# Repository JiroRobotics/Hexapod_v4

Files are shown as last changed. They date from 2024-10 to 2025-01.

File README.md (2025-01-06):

# Hexapod v4
Check out the YouTube video: https://youtu.be/cIIxmBn0WJ8

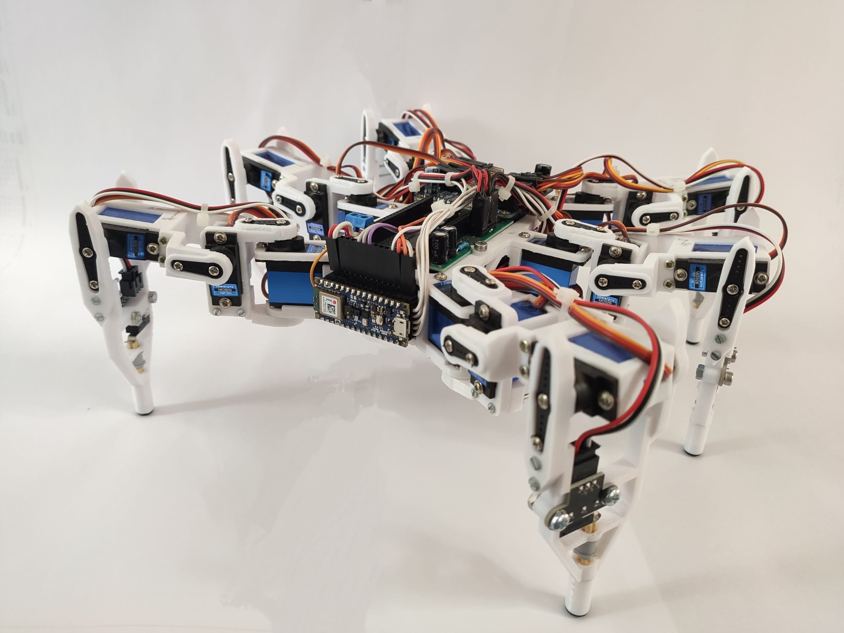
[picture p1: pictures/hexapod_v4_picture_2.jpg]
Hexapod prototype


## Quickstart

1. Build your Hexapod
2. Download this repository as well as all other necessary libraries
3. Change angle() and angleFloat() in Leg.cpp to use the correct pulse lengths for your servos. The current configuration works for (one type of) MG92b servos.
4. The isReachable() method of the Leg class is highly dependent on the geometry of your robot, therefore it also needs to be changed if you don't use the CAD files.
5. Take a close look at Config.h and change all values accordingly. You'll need to change all pins as well as all measurements.
6. Also change the addresses of your servo drivers to the correct hex value.
7. Double check your wiring and provide the Leg() constructors in Hexapod_v4.ino with the correct PWM Module.
8. Figure out the offsets for each servo. If you write an angle of 90° to a servo, the corresponding joint should form a right angle. Keep these offsets as low as possible (-10° to 10°). You might also need to unscrew the joint and mount it at a different angle.
9. The code works well on an Arduino Nano 33 BLE Sense. If you use other, less capable Arduinos like Nano 33 IOT, you might need to increase the periodMS setting in Config.h, until the Arduino is able to calculate everything in this time frame.

## Background

Hexapods are six legged robots. They possess the ability to walk in any direction, each leg (in this case) with three joints resulting in a total of 18 degrees of freedom. In addition, their body can turn and rotate in any direction, making this type of legged robot extremely flexible. But six legs also allow for fast, statically determined walking gates, i.e. lifting three legs each step while the three other legs stay on the ground. This removes the challenge of balancing during one step. 

As written in the title, this project is my fourth hexapod robot. It uses largely the same hardware as the previous generation but the code was rewritten entirely. The ReadMe was written in order to provide support and document the whole project. Feel free to contact me for questions/suggestions/improvements.

## Requirements

In addition to the code in this repository, you will need two additional libraries, "Adafruit_PWMServoDriver.h" and "Arduino_BMI270_BMM150.h" for the servo driver and the IMU (only Arduino Nano 33 BLE) respectively. Just clone this repository and adjust the code to suit your robot. Almost all important constants are specified in Config.h, but a few other things also need to be changed, e.g. the constraints for leg movement (more on that later) or the servo pulse lengths. This ReadMe is written in a way which should allow you to follow my thought process during the creation of this robot. It is quite extensive so don't be afraid to skip some parts. The code is mathematically challenging, so you should be familiar with the basics of inverse kinematics and coordinate transformation in order to understand everything.

## Hardware

The robot is comprised of a 3D-printed body and six legs. The four corner legs are turned by an angle of 30° relative to the middle legs, thus requiring more complex code. Consider mounting the corner legs parallel to the middle legs in your project to avoid the need for more coordinate transformation in your code. 
Each leg consists of three joints and three links refered to as coxa, femur and tibia. Each joint is directly screwed to the servo on one side and on the other a tiny bearing is used to reduce friction, add strength and avoid wear and tear.
The coxa link incorporates a limit switch to detect whether the leg is touching the ground. If the leg is touching the ground, the weight doesn't rest on the switch but the surrounding structure.

As for the electronics, the robot is powered by 18 TowerPro MG92b servo motors. As the name suggests, these servos use metal gears as well as a small bearing on the shaft, making them pretty robust and ideal for the use in this application. Nine servos are each connected to an [Adafruit PCA9685 16-Channel Servo Driver](https://learn.adafruit.com/16-channel-pwm-servo-driver/downloads), resulting in one servo driver for each side (left/right) of the robot. Make sure to use the original Adafruit servo driver since the cheaper alternatives often use a low-quality MOSFET which is not suitable for providing enough current for 18 servo motors. They are often marketed as LED-drivers only.
A 10V 1000uF capacitor is used as suggested by Adafruit to avoid voltage dips when all servos move at the same time, minimizing the chance for brownouts. The two servo drivers are connected to an Arduino Nano 33 BLE Sense Rev2 via I2C. Make sure that you power the servo motors not through the Arduino but directly from the power source (using the V+ pin on the board). In this robot, I used a rechargeable 6V 3000mAh NiMH-Battery which provides plenty of power while lasting a good 20-30 minutes. A large switch on the back of the robot acts as the killswitch, immediatly cutting power from the Arduino as well as the drivers.
The six limit switches are also connected to the Arduino using six of the GPIOs. Additionally, an ESP32 (potentionally with an integrated camera module) can be placed on top of the robot to stream a video feed of what the robot sees directly on your phone.

## Software
The code for this robot was entirely written in C++ (or rather the Arduino version of C++). The rough structure is as follows:
* A Leg class which handles the inverse kinematics of each leg (only the movement in the local coordinate system of each leg). This class also checks whether or not a (x, y, z) point is reachable for the end point of the leg and if the leg is touching the ground.
* A Hexapod class which is an aggregation of six leg instances. This class covers all movement patterns (such as crab walk, translation and rotation on the spot, turning, ...).
* The main Arduino programm, which is comprised of the setup() and the loop()-part. The setup()-part is run once and covers all the initialization of the servo drivers as well as setting pin modes, starting the IMU and so on. The loop() function is coded so that it is executed every 10ms, giving the hexapod an update rate of 100Hz. This means that the leg positions are calculated and the legs are moved to their positions every 10ms or 100 times a second. Running a fixed update rate allows for more flexible movement as a step is not necessarily excecuted as a whole and other movements can be superimposed.

Let's take a look at the math-heavy challenges for this project:

### Inverse Kinematics Of One Leg
**Goal:** given a point (x, y, z) in the local coordinate frame of the leg, calculate the joint angles of the three servo motors so that the end point of the leg reaches the desired point
First, we assume that the point is valid/reachable (more on that later). Next we will have to take a look at the coordinate system and how the leg is positioned in it.

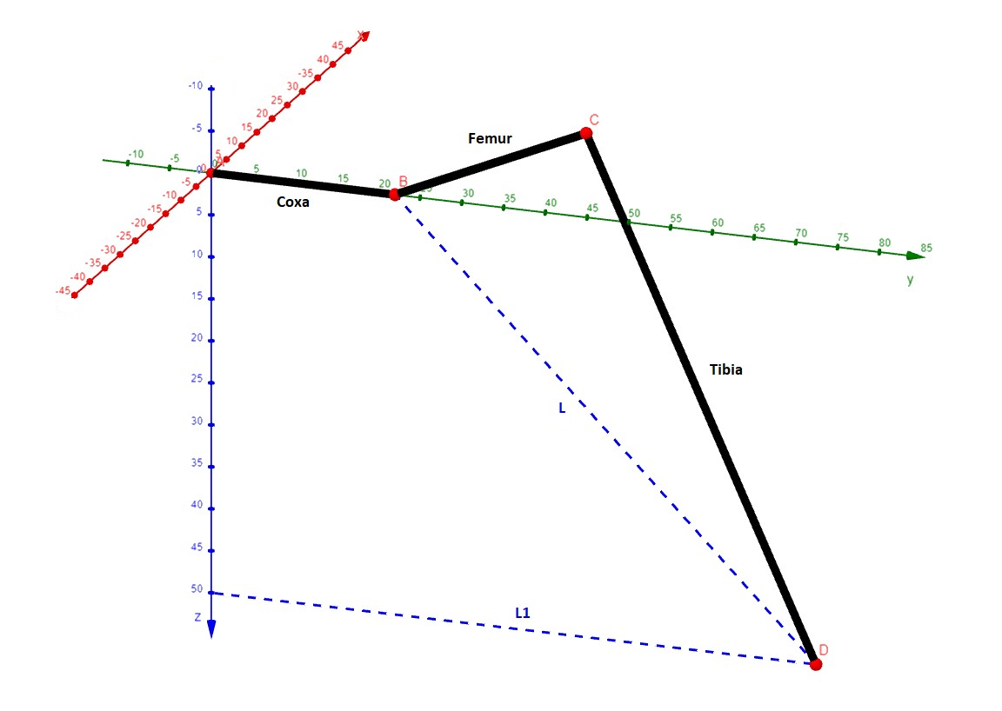
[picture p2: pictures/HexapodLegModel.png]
Image of a leg model and the coordinate system as well as L and L1


A, B and C are the coxa, femur and tibia joints while D is the desired point given in (x, y, z) coordinates. It becomes apparent that the coxa angle is only dependent on the x and y and can be calculated by using the atan2(y, x) function. Note that this returns radians, so you might need to convert to degrees. Perhaps you also need to mirror the value using map(), depending on the servo orientation.
The values for the femur and tibia joint are a bit more complex. First, we need to calculate two distances: L1 and L. L1 is simply the distance from the z-axis to point D, which can be found using the pythagorean theorem. L1 can than be used to calculate L, which is the distance from B to D. Again, it is found by using the pythagorean theorem. Now, by applying the law of cosine, the angles of the triangle BCD can be found. Make sure to shift/mirror the values to match the orientation of the servos. The code for calculating all three angles is as follows:

```
float coxaAngle = atan2(yValue, xValue) * 180 / PI;
coxaAngle = map(coxaAngle, 0, 180, 180, 0);
float femurAngle = (acos(zValue / L) + acos((tibiaLength * tibiaLength - femurLength * femurLength - L * L) / (-2 * femurLength * L))) * 180 / PI;
float tibiaAngle = (acos((L * L - tibiaLength * tibiaLength - femurLength * femurLength) / (-2 * tibiaLength * femurLength))) * 180 / PI;
```

The last thing to do is to actually move the servos. This can be achieved by calling the following line:

```
servoDriver.setPWM(pinCoxa, 0, angleFloat(coxaAngle + offsetCoxa));
```
angleFloat() is a function to convert the angle in degrees to the corresponding pulse width of the PWM signal (also described in the Adafruit Servo Driver documentation). The values in angleFloat() have to be adjusted if another type of servo is used. offsetCoxa is the offset (in degrees) by which the (real) position of the leg differs compared to the ideal position. Find these values by assembling the robot, setting all servos to for example 90° and adjust the offsets until all joints are perfectly perpendicular.

### Calculating Valid Points
The leg can't reach every (x, y, z) point in 3D space. If we instruct the leg to move to an unreachable point, weird things can happen, potentionally even breaking the robot. Even if all points passed to the leg function _should_ be reachable, it is recommended to implement the following as a last safeguard:
The constrains for the coxaAngle parameter can be chosen by simply measuring how far the legs can rotate before hitting the neighboring leg rotating in the opposite direction. In this case, coxaAngle can only be in the interval [40°, 130°]
Instead of implementing constrains directly for tibiaAngle and femurAngle, we simply look at the L1 value and the z value and define an area in which L1 and z have to be to be valid. This area can be found mathematically or approximated using a CAD model (as shown in the image). By comparing L1 and z to the upper and lower bound, each point can be verified.

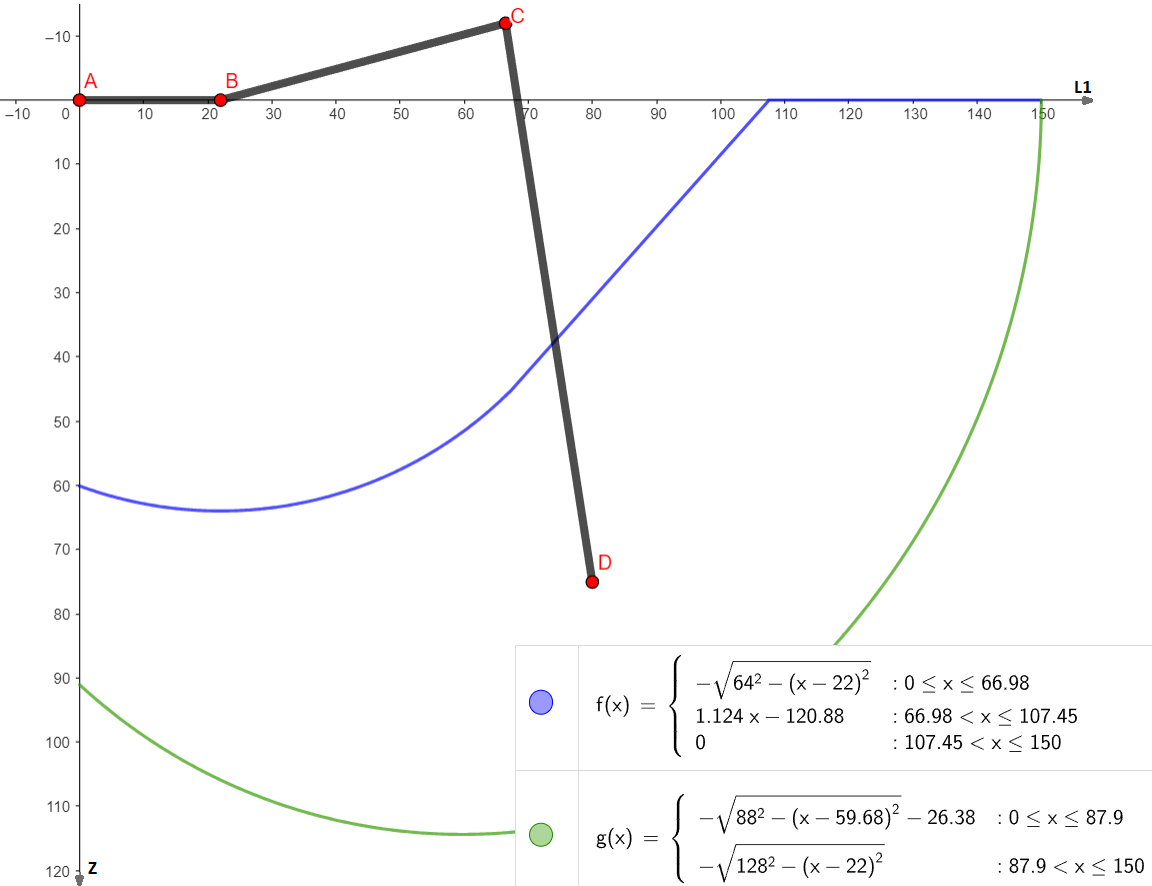
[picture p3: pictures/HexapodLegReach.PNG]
Image of the area reachable by one leg


### The Hexapod Class
As mentioned above, the six leg classes are passed to one Hexapod class which coordinates the legs and calculates all necessary points in the (local) coordinate system for each leg. The Hexapod class contains multiple methods for moving the robot:
* **moveLegs():** This elementary method moves all six legs to their positions as specified in the array, if they are reachable.
* **calcBodyMovement():** This method has six parameters (and two pointers to the leg position arrays). Namely three (x-, y-, z-) translation values and three (roll, pitch, yaw) rotation values. The robot center (the base coordinate system) is moved to match the given parameters, while all legs remain at their current position in the global coordinate frame. For example, a translation of xTrans = 30 means that the center of mass of the robot is shifted by 30mm to the front compared to home position, while an angle of roll = 0.2 (in radians) tilts the robot by approx. 11.5° sideways. Note that this method doesn't actually move the legs but rather calculates the positions of all legs and writes them in the <code>newPositions[][]</code> array. The moveLegs() method has to be called to actually move the legs.
* **calcStep():** Universal method which lets the robot walk. It should be called periodically as many times as specified in stepNumber. In the first iteration, the final coordinates for each leg at the end of the step are calculated. In the following iterations, the current position is interpolated between the starting position and the final position. 
* **Offroad mode:** Still needs to be implemented. Using the end switches, the robot will detect whether its legs touch the surface and adjust the z coordinate accordingly.

### Calculating Points For Each Leg
The position and orientation of the different coordinate frames can be seen in the picture below. The coordinate frame in the center of the robot is referred to as base coordinate system, which is identical to the global coordinate system at the start. The six local coordinate frames have their origin in the coxa joint of their leg respectively. 

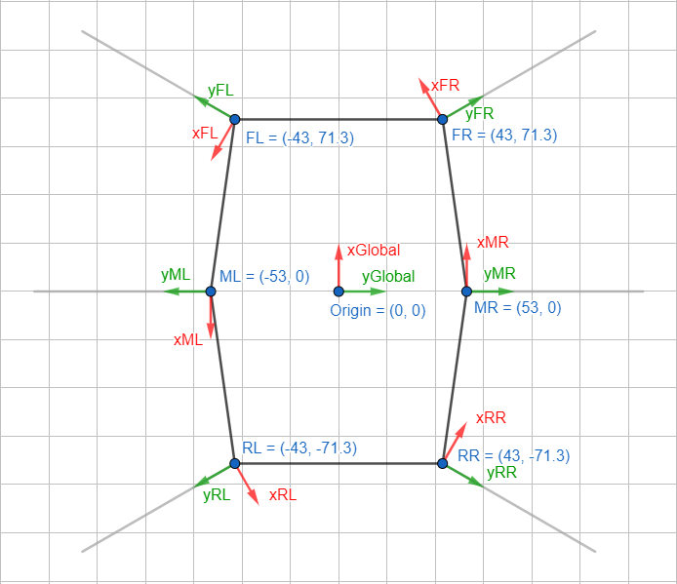
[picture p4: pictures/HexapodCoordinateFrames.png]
Image of the global and the six local coordinate systems


The Leg class can only work with coordinates in the local coordinate system of the leg, while the motion planning takes place in the global or base coordinate system. Therefore we need to transform between the coordinate frames. This can be done in multiple ways, for example using rotation matrices and shifting of the planes. 

To calculate the new end point of a leg in the local coordinate frame resulting from a translation along one of the axis of the base coordinate frame, we first need to shift and rotate the local frame to match the frame in the center of mass. To keep the code simple, an array is used to store the relative distances and angles between the local coordinate frame of each leg and the base coordinate system. This array (<code>legCoords[][]</code>) is specified in [Config.h](Config.h).

Now, the desired translation and rotation can be applied. First, the end point is shifted by the desired amount to achieve the translation. Second, the point is rotated by multiplying it with rotMatrix[][], which is a complete 3x3 roll pitch yaw rotation matrix.
At last, the local coordinate frame has to be transformed back, first shifting it and then rotating it.

```
for (uint8_t k = 0; k < 6; ++k) {  // iterate over all legs

    // check if the leg should move (0b100000 is FR, 0b010000 is FL, ... 0b000001 is RL)
    if (legMask & (1 << (5 - k))) {

      // rotate the local coordinate system by the angle specified in legCoords[][]
      int temp = newPositions[k][0];
      newPositions[k][0] = newPositions[k][0] * cos(-legCoords[k][2]) - newPositions[k][1] * sin(-legCoords[k][2]);
      newPositions[k][1] = temp * sin(-legCoords[k][2]) + newPositions[k][1] * cos(-legCoords[k][2]);

      //shift the local coordinate system to the center of mass
      newPositions[k][0] += legCoords[k][0];
      newPositions[k][1] += legCoords[k][1];

      // translation of leg end point
      newPositions[k][0] -= xTrans;
      newPositions[k][1] -= yTrans;
      newPositions[k][2] += zTrans;

      // rotating the end point using RotMatrix
      float result[3] = { 0.0, 0.0, 0.0 };

      for (int i = 0; i < 3; ++i) {
        for (int j = 0; j < 3; ++j) {
          result[i] += (rotMatrix[i][j] * newPositions[k][j]);
        }
      }
      for (int i = 0; i < 3; ++i) {
        newPositions[k][i] = result[i];
      }

      //shift the local coordinate system back
      newPositions[k][0] -= legCoords[k][0];
      newPositions[k][1] -= legCoords[k][1];

      //rotate the coordinate system back by the mounting angle of the leg
      temp = newPositions[k][0];
      newPositions[k][0] = newPositions[k][0] * cos(legCoords[k][2]) - newPositions[k][1] * sin(legCoords[k][2]);
      newPositions[k][1] = temp * sin(legCoords[k][2]) + newPositions[k][1] * cos(legCoords[k][2]);
    }
}
```

The code above iterates over all legs. The bitmask allows only specific legs to move. As standard, all legs are moved (<code>legMask = 0b111111</code>). The first bit (MSB) corresponds to the front right leg, the last bit (LSB) to the rear left leg.

Improvements/additions would be to use quaternions for faster computation of the rotations or to just use 4x4 homogeneous matrices to first transform the coordinate frames and then calculate the translation and rotation in one step (and then transforming the frame back of course).

### Walking In Any Direction
Two approaches exist to create a walking motion in any direction (aka crab walk). Both approaches lift three legs, while the other three legs move the body. For example, the front left, middle right and rear left legs are being lifted, while the front right, middle left and rear right legs push the hexapod in the desired direction. The first version is simpler, but doesn't allow for long step distances, thus resulting in a more "unnatural" motion:
> [!NOTE]  
> The code for this approach can be found in the "deprecated" branch.

A "home position" is defined (in the local coordinate frame, as an (x, y, z) point), to which the three legs which were lifted return after every step. As a result, three legs are guaranteed to be at the home position in the beginning of each step. From there, new points are calculated for each of the three legs. These new points describe the final position of the legs at the end of the step. The other legs (which were previously **not** at home position) just return to home position.
Final positions for the three legs can be calculated by simply transforming (rotating) the vector by which the hexapod moves in the local coordinate system and then subtracting the vector from the home position. This vector can be passed to the method as two parameters, namely stepDist and stepDirection. stepDist is the length of the vector by which the hexapod moves while stepDirection is the angle, in which the step is taken (simply a 2D-vector in polar coordinates). For example, <code>stepDist = 20</code> and <code>stepDirection = PI</code> will result in a step with a length of 20mm backwards (PI (rad) = 180°).
While providing a simple form of movement, which is also quite flexible (all possible steps can be executed after a step, the step length and direction is known, ...), it looks pretty unnatural. In addition, the maximum step length is short with only around 40mm. To achieve longer steps with more natural movement, another approach can be taken:

In this approach, a "home position" is defined also. The leg isn't actually moved to the home position, but the position is used to construct a circle, in which the leg operates at every point in time. The size of the circle will later determine the maximum step length. The difference in comparison to the previous approach is the position at which the legs are after every step (obviously, duh...). After one step **all six** legs will be on the circumference of the circle. The three legs moving the hexapod will move from their current position in the given direction, until they hit the boundary of the circle. The three legs which were returning to home position in the previous approach will now be lifted and moved in the opposite direction until they hit the boundary of the circle, thus allowing the *next* step to be of maximum length. One can simply notice, that the maximum length can only be achieved if the next step is taken in the same direction as the previous (or the exact opposite direction) and, in the worst case, no movement is possible at all. This worst case occurs if the next step's direction is exactly 90° from the previous step. By keeping track of the previous step direction, the pair of legs which can perform the longest step in the new direction can be determined. Therefore, the difference between the previous and the new direction is considered. If the difference is smaller than 90°, the other set of legs is moved (e.g. if in the previous step, legs front right, mid left and rear right moved the robot and the new direction is 45° larger than in the previous step, the other set of legs will now move the robot). If the difference is larger than 90°, the same set of legs which performed the previous step will also perform the next step, as they can move the longest distance.

Up until now, the robot can walk in all directions, but can't rotate in any form. To fix this, a trick can be used: After all final positions for the current step are calculated, these final positions can be rotated. Using the calcBodyMovement() method along with a mask, a rotation (yaw) is applied to the three legs which move the robot. While this allows the robot to move in any direction with any rotation superimposed, it also means that the final positions are not guaranteed to be inside of the circle anymore. Therefore, other precautions must be taken to avoid unwanted behaviour.

```
if ((overlayRotation > 0.02 && overlayRotation < 0.3) || (overlayRotation < -0.02 && overlayRotation > -0.3)) {  // avoid too crazy turn angles and unnecessary calculation
  uint8_t mask = 0b100110;                                                                                       // apply rotation only to the stationary legs FR, ML, RR
  if (moveRightLeg == false) {
    mask = 0b011001;  // change if the other set of legs (FL, MR, RL) if they are stationary
  }
  calcBodyMovement(finalPositions, finalPositions, 0, 0, 0, 0.0, 0.0, overlayRotation, mask);
}
```
### Balancing
If the Arduino you are using also has a built-in IMU, the robot can also balance itself. The current code only supports the IMU of the Arduino Nano 33 BLE Rev2 altough very few changes should be necessary to make it work using a Nano 33 IoT or similar. If you use your own sensor or layout, make sure that the calculation of roll and pitch angles in <code>readRollPitch()</code> and <code>calibrateIMU()</code> is correct (due to possibly different orientation of the IMU coordinate system).
<br> When starting the robot, the IMU first needs to be calibrated. The offsets need to be adjusted to get a reference data in level position. This is done by taking 1000 samples, calculate the average and storing these values as offsets. After calibrating, the robot is able to calculate roll and pitch values at any moment in time. To get rid of noise in the data, a simple IIR low pass filter is used. Because of this, the  <code>readRollPitch()</code> or the <code>balance()</code> method should be called often, idealy with a fixed period. The control loop block diagram can be seen in the picture below.

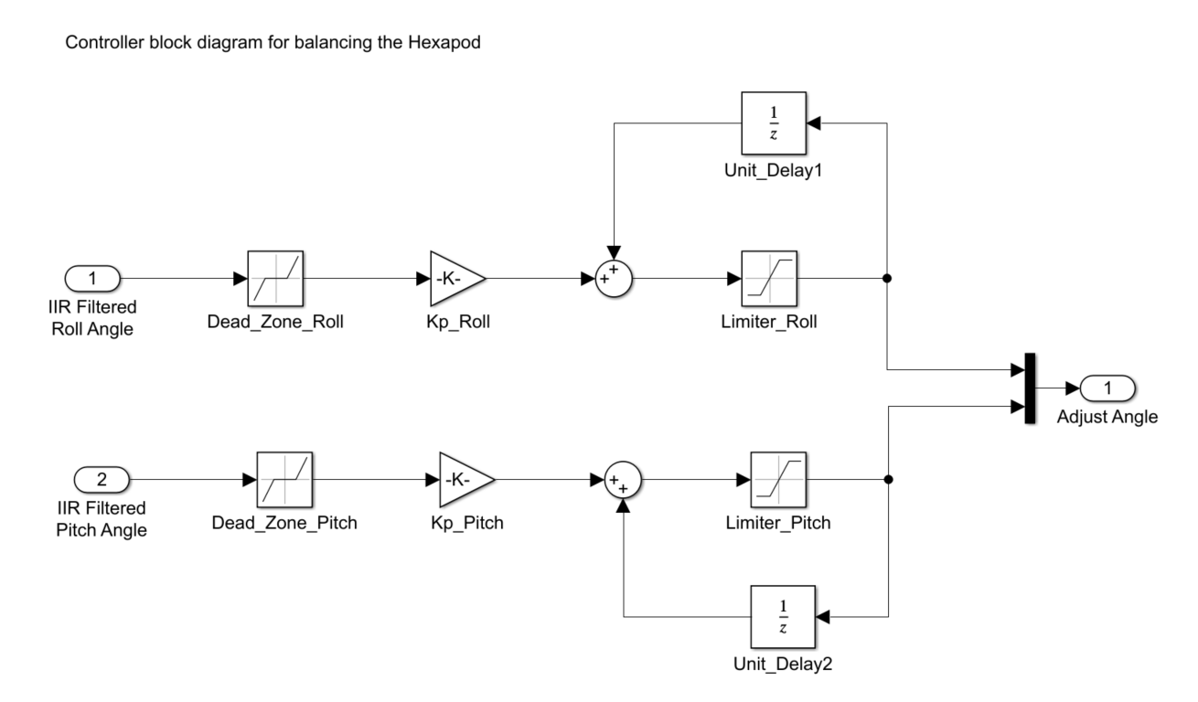
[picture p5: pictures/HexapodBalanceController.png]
Block diagram of the balance controller


After calculating new roll and pitch output values, these values are passed to the <code>calcBodyMovement()</code> method, which calculates new leg positions wo compensate for the measured angles.
> [!NOTE]  
> Getting data from the IMU is quite slow (~5ms). Therefore, one iteration with <code>myHexapod.balance()</code> and <code>myHexapod.calcBodyMovement()</code> might take longer than 10ms (the default value for <code>periodMS</code>

It is also possible to take steps while balancing, see <code>exampleBalanceAndStep()</code> for more details.

### Path Following
The <code>myHexapod.travelPath()</code> method allows the user to specify multiple target points in the global x-y-plane which the robot will try to reach one after another. Note that this method is blocking and therefore shouldn't be called together with other methods like <code>myHexapod.calcStep()</code> or <code>myHexapod.moveLegs()</code>. Two different modes for path following exist, one where the robot walks in any direction while maintaining the same heading (like a crab) and one where the robot only walks forward and rotates if necessary. The more points the hexapod travels to, the higher the inaccuracy in position and heading becomes. <code>rotateAccuracy</code> and <code>lengthAccuracy</code> are two parameters you can adjust to get better results.
### Main Loop
As already mentioned, the <code>loop()</code> function is called every 10ms (or as specified in Config.h). During each loop iteration, the legs are moved once using <code>myHexapod.moveLegs(newPositions)</code>. <code>newPositions[][]</code> can be can be calculated using either <code>myHexapod.calcStep()</code>, <code>myHexapod.calcBodyMovement()</code> or both. Example usage is provided in <code>exampleSteps()</code> and <code>exampleBodyMovement()</code>. The <code>myHexapod.getAction()</code> method can be used to check whether the robot is executing a step or resting at the moment. Additionally, a loopCounter is used to keep track of the number of times the loop has been executed. The green LED of the Arduino BLE is also toggled in every loop (yellow LED on other Arduinos).

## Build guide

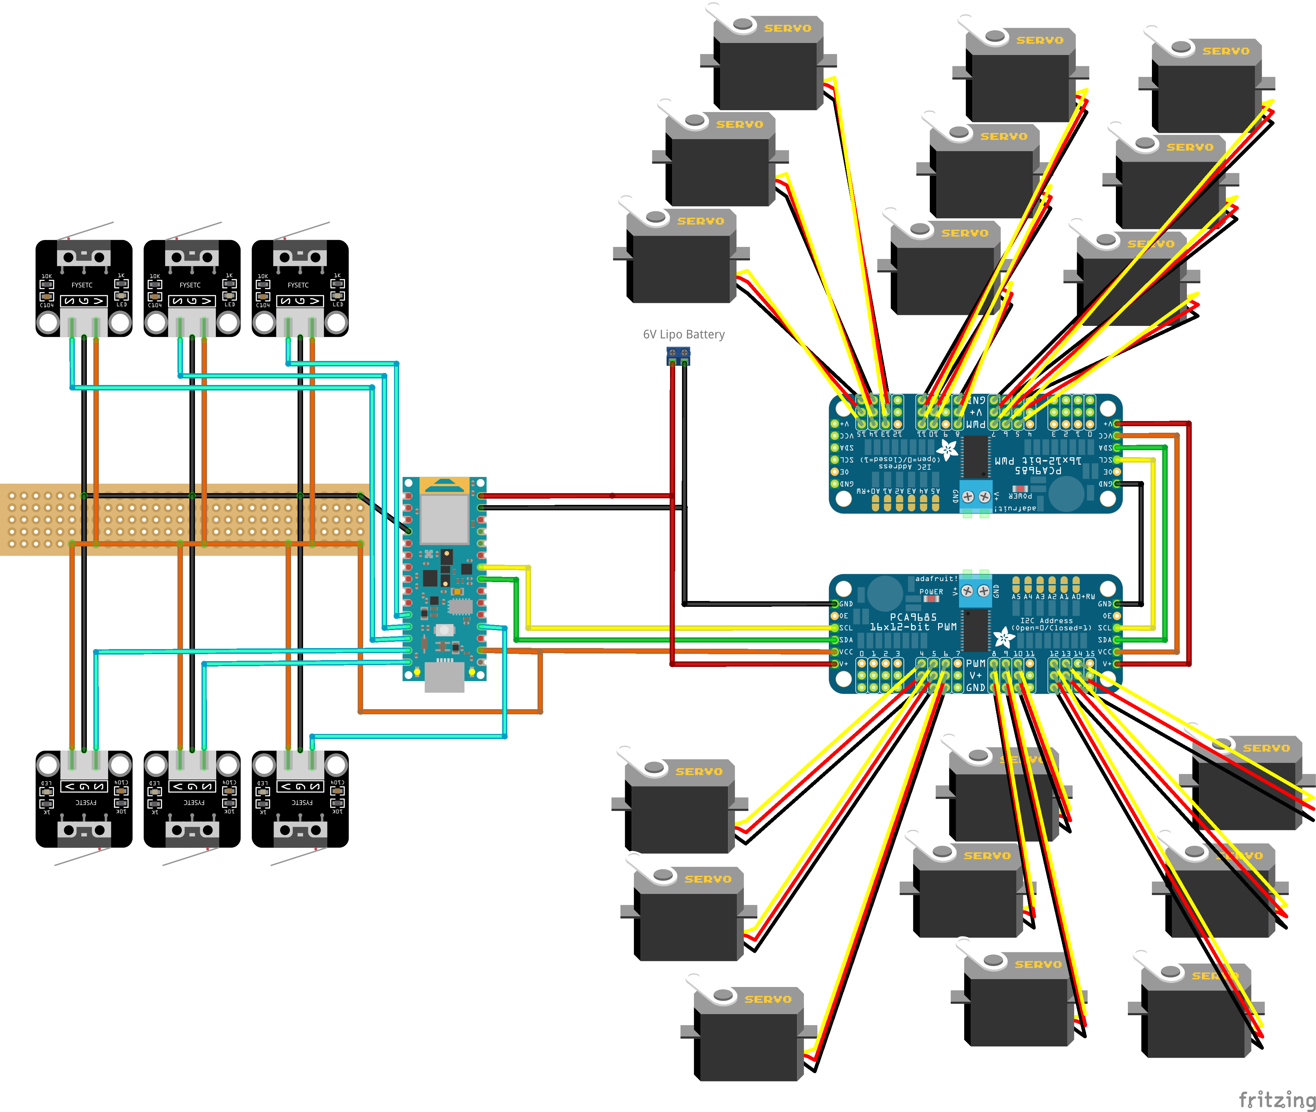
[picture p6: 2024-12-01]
resources/wiring_diagram.png

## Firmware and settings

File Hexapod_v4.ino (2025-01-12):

// 4th generation Hexapod
// Hardware is largely the same as v3. Currently uses a Nano 33 BLE Sense Rev 2, but will also work on other capable
// Arduinos like the Nano 33 IoT

//#define DEBUG

#include <Arduino_BMI270_BMM150.h>
#include <Adafruit_PWMServoDriver.h>
#include "Config.h"
#include "Hexapod.h"
#include "Leg.h"

Adafruit_PWMServoDriver pwm1 = Adafruit_PWMServoDriver(pwm1Addr);
Adafruit_PWMServoDriver pwm2 = Adafruit_PWMServoDriver(pwm2Addr);

// initialize all six legs of the robot using config.h
Leg legFrontRight = Leg(pwm2, coxaPinFR, femurPinFR, tibiaPinFR, coxaOffsetFR, femurOffsetFR, tibiaOffsetFR, true, buttonFR);
Leg legFrontLeft = Leg(pwm1, coxaPinFL, femurPinFL, tibiaPinFL, coxaOffsetFL, femurOffsetFL, tibiaOffsetFL, false, buttonFL);
Leg legMidRight = Leg(pwm2, coxaPinMR, femurPinMR, tibiaPinMR, coxaOffsetMR, femurOffsetMR, tibiaOffsetMR, true, buttonMR);
Leg legMidLeft = Leg(pwm1, coxaPinML, femurPinML, tibiaPinML, coxaOffsetML, femurOffsetML, tibiaOffsetML, false, buttonML);
Leg legRearRight = Leg(pwm2, coxaPinRR, femurPinRR, tibiaPinRR, coxaOffsetRR, femurOffsetRR, tibiaOffsetRR, true, buttonRR);
Leg legRearLeft = Leg(pwm1, coxaPinRL, femurPinRL, tibiaPinRL, coxaOffsetRL, femurOffsetRL, tibiaOffsetRL, false, buttonRL);

// Initialization of hexapod object
Hexapod myHexapod = Hexapod(legFrontRight, legFrontLeft, legMidRight, legMidLeft, legRearRight, legRearLeft);

// arrays which store the positions of each leg in x-y-z local coordinates
// stores local leg positions after each completed step
float legPositions[6][3] = { { homePos[0], homePos[1], homePos[2] },    // front right
                             { homePos[0], homePos[1], homePos[2] },    // front left
                             { homePos[0], homePos[1], homePos[2] },    // mid right
                             { homePos[0], homePos[1], homePos[2] },    // mid left
                             { homePos[0], homePos[1], homePos[2] },    // rear right
                             { homePos[0], homePos[1], homePos[2] } };  // rear left

// preliminary leg positions before applying additional body movement
float currPositions[6][3];
// final leg positions for one iteration, passed to moveLegs()
float newPositions[6][3];

// keeps track of steps taken
uint16_t counter = 0;
// keeps track of number of iterations
unsigned long loopCounter = 0;

// allows for basic path following
const uint8_t numberPoints = 4;
int16_t waypoints[numberPoints][2] = { { 500, 0 },
                                       { 700, 300 },
                                       { 400, 800 },
                                       { 400, 1200 } };

void setup() {

#ifdef ARDUINO_ARDUINO_NANO33BLE
  pinMode(LEDR, OUTPUT);
  pinMode(LEDB, OUTPUT);
  pinMode(LEDG, OUTPUT);

  // Built in RGB is inverted
  digitalWrite(LEDR, HIGH);
  digitalWrite(LEDB, HIGH);
  digitalWrite(LEDG, HIGH);
#endif
  // use the builtin LED on pin 13 as an OUTPUT
  pinMode(LED_BUILTIN, OUTPUT);
  digitalWrite(LED_BUILTIN, LOW);

#ifdef DEBUG
  // used for debug
  Serial.begin(9600);
#endif

  // start pwm on the servo drivers with 50Hz frequency
  pwm1.begin();
  pwm1.setPWMFreq(50);
  pwm2.begin();
  pwm2.setPWMFreq(50);

  // move all legs to their home position
  myHexapod.moveHome();

  // start the internal IMU (Nano 33 BLE only)
  myHexapod.startIMU();

  myHexapod.calibrateIMU();
  delay(1000);
}

void loop() {

  // get the current time
  unsigned long timeMillis = millis();

  // exemplary movements of the robot
  // uncomment one of the following
  //exampleBodyMovement();
  //exampleSteps();
  //exampleSteps2();
  //exampleBalanceAndStep(); // only Arduino Nano 33 BLE
  exampleOffroad();
  


  // The path travel method is blocking and handles everything internally (moving legs etc.).
  //myHexapod.travelPath(legPositions, waypoints, numberPoints, 120, 0, 0.2, 35);
  //while(true){} // wait after reaching the last point

  // update the leg position
  myHexapod.moveLegs(newPositions);

  // increment the loopCounter to keep track of the number of loop cycles
  loopCounter++;
  if (loopCounter == 2500) {
    loopCounter = 0;
  }

#ifdef ARDUINO_ARDUINO_NANO33BLE
  if (loopCounter % 2) {  // turn the led on and of to show each loop iteration
    digitalWrite(LEDG, HIGH);
  } else {
    digitalWrite(LEDG, LOW);
  }
#else
  if (loopCounter % 2) {  // turn the led on and of to show each loop iteration
    digitalWrite(LED_BUILTIN, HIGH);
  } else {
    digitalWrite(LED_BUILTIN, LOW);
  }
#endif

#ifdef DEBUG
  // Make sure that the arduino is fast enough to calculate everything in periodMS time span
  unsigned long millisCalc = millis();
  Serial.print("Time calculated:");
  Serial.println(millisCalc - timeMillis);
  while (millis() < timeMillis + periodMs) {
    // wait a bit so that the loop is executet every periodMS ms
  }
  Serial.print("Time waited:");
  Serial.println(millis() - millisCalc);
#else
  while (millis() < timeMillis + periodMs) {
    // wait a bit so that the loop is executet every periodMS ms
  }
#endif
}





void exampleSteps() {
  /*
   * Example usage of calcStep(). Does a couple of steps in different directions.
   * counter keeps track of number of steps.
   * 
   * calcBodyMovement() would also allow for body movement while walking.
   */
  // keep track of the number of steps
  if (myHexapod.getAction() == 0) {
    // increase the counter each time the robot is resting
    counter++;
    if (counter == 25) {
      counter = 0;
    }
  }

  // do a couple steps in different directions
  if (counter < 5) {
    myHexapod.calcStep(legPositions, currPositions, 0, 30, 120, 0.0, 20);
  } else if (counter < 15) {
    myHexapod.calcStep(legPositions, currPositions, PI / 2, 20, 120, 0.15, 20);
  } else if (counter < 20) {
    myHexapod.calcStep(legPositions, currPositions, 0, 20, 120, 0.15, 20);
  } else {
    myHexapod.calcStep(legPositions, currPositions, PI, 3, 120, -0.2, 20);
  }

  // Adjust the body position each loop() iteration. This allows for superimposition of body movement independently of the step
  myHexapod.calcBodyMovement(currPositions, newPositions, 0, 0, 0, 0.0, 0.0, 0.0);
}




void exampleSteps2() {
  /*
   * Example usage of calcStep()
   * Walks in a straight line while rotating the robot simultaneously
   *
   * calcBodyMovement() would also allow for body movement during execution
   */
  // keep track of the number of steps
  if (myHexapod.getAction() == 0) {
    // increase the counter each time the robot is resting
    counter++;
    if (counter == 21) {
      counter = 0;
    }
  }
  float newDir = PI - (counter - 1) * 0.15;
  myHexapod.calcStep(legPositions, currPositions, newDir, 20, 120, 0.15, 20);

  // Adjust the body position each loop() iteration. This allows for superimposition of body movement independently of the step
  myHexapod.calcBodyMovement(currPositions, newPositions, 0, 0, 0, 0.0, 0.0, 0.0);
}




void exampleBalanceAndStep(){
  /*
   * Example usage of balance() in combination with calcStep().
   * Slowly walks in a straight line while constantly adjusting roll and pitch of calcBodyMovement() to keep the body level.
   *
   * NOTE: only works on the Arduino Nano BLE Sense for now, Nano 33 IoT requires different library but is also possible
   * NOTE: IMU is fairly slow (~5ms to get data). Therefore might take longer than the usual 10ms cycle.
   */
  myHexapod.calcStep(legPositions, currPositions, 0, 20, 150, 0.0, 20);
  myHexapod.balance(currPositions, newPositions);
}

void exampleOffroad(){
  /*
   * Uses the built in buttons in each leg to determine whether the leg touches the ground. This allows the robot to walk over uneven terrain
   * Slowly walks in a straight line, while constantly adjusting roll and pitch to keep the body level.
   *
   * NOTE: only works on the Arduino Nano BLE Sense for now, Nano 33 IoT requires different library but is also possible
   * NOTE: IMU is fairly slow (~5ms to get data). Therefore might take longer than the usual 10ms cycle.
   */
  myHexapod.calcStep(legPositions, currPositions, 0, 20, 70, 0.0, 30, true);
  myHexapod.balance(currPositions, newPositions);
}


void exampleBodyMovement() {
  /* 
   * Example usage of calcBodyMovement to move the robots body.
   * loopCounter keeps track of number of loop()-iterations.
   *
   * moves (translation and rotation) the robots body.
   */

  if (loopCounter < 150) {
    int b = map(loopCounter, 0, 150, 0, 180);
    myHexapod.calcBodyMovement(legPositions, newPositions, 0, 0, 0, 0.0, b / 1000.0, 0.0);

  } else if (loopCounter < 250) {
    myHexapod.calcBodyMovement(legPositions, newPositions, 0, 0, 0, 0.0, 0.15, 0.0);

  } else if (loopCounter < 400) {
    int b = map(loopCounter, 250, 400, 180, -180);
    myHexapod.calcBodyMovement(legPositions, newPositions, 0, 0, 0, 0.0, b / 1000.0, 0.0);

  } else if (loopCounter < 500) {
    myHexapod.calcBodyMovement(legPositions, newPositions, 0, 0, 0, 0.0, -0.18, 0.0);

  } else if (loopCounter < 650) {
    int b = map(loopCounter, 500, 650, -180, 0);
    myHexapod.calcBodyMovement(legPositions, newPositions, 0, 0, 0, 0.0, b / 1000.0, 0.0);

  } else if (loopCounter < 800) {
    int b = map(loopCounter, 650, 800, 0, 150);
    myHexapod.calcBodyMovement(legPositions, newPositions, 0, 0, 0, b / 1000.0, 0.0, 0.0);

  } else if (loopCounter < 950) {
    int b = map(loopCounter, 800, 950, 150, -150);
    myHexapod.calcBodyMovement(legPositions, newPositions, 0, 0, 0, b / 1000.0, 0.0, 0.0);

  } else if (loopCounter < 1100) {
    int b = map(loopCounter, 950, 1100, -150, 0);
    myHexapod.calcBodyMovement(legPositions, newPositions, 0, 0, 0, b / 1000.0, 0.0, 0.0);

  } else if (loopCounter < 1250) {
    int b = map(loopCounter, 1100, 1250, 0, 20);
    myHexapod.calcBodyMovement(legPositions, newPositions, 0, 0, b, 0.0, 0.0, 0.0);

  } else if (loopCounter < 1350) {
    myHexapod.calcBodyMovement(legPositions, newPositions, 0, 0, 20, 0.0, 0.0, 0.0);

  } else if (loopCounter < 1500) {
    int b = map(loopCounter, 1350, 1500, 20, -20);
    myHexapod.calcBodyMovement(legPositions, newPositions, 0, 0, b, 0.0, 0.0, 0.0);

  } else if (loopCounter < 1600) {
    myHexapod.calcBodyMovement(legPositions, newPositions, 0, 0, -20, 0.0, 0.0, 0.0);

  } else if (loopCounter < 1750) {
    int b = map(loopCounter, 1600, 1750, -20, 0);
    int c = map(loopCounter, 1600, 1750, 0, 20);
    myHexapod.calcBodyMovement(legPositions, newPositions, c, 0, b, 0.0, 0.0, 0.0);

  } else if (loopCounter < 2000) {
    int b = round(20.0 * sin(loopCounter * 2.0 * PI / 250.0));
    int c = round(20.0 * cos(loopCounter * 2.0 * PI / 250.0));
    myHexapod.calcBodyMovement(legPositions, newPositions, c, b, 0, 0.0, 0.0, 0.0);

  } else if (loopCounter < 2100) {
    int c = map(loopCounter, 2000, 2100, 20, 0);
    myHexapod.calcBodyMovement(legPositions, newPositions, c, 0, 0, 0.0, 0.0, 0.0);

  } else if (loopCounter < 2250) {
    int b = map(loopCounter, 2100, 2250, 0, 150);
    myHexapod.calcBodyMovement(legPositions, newPositions, 0, 0, 0, b / 1000.0, b / 1000.0, 0.0);

  } else if (loopCounter < 2400) {
    int b = map(loopCounter, 2250, 2400, 150, 0);
    myHexapod.calcBodyMovement(legPositions, newPositions, 0, 0, 0, b / 1000.0, b / 1000.0, 0.0);

  } else {
    myHexapod.calcBodyMovement(legPositions, newPositions, 0, 0, 0, 0.0, 0.0, 0.0);
  }
}

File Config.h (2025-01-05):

// Config.h

#ifndef Config_H
#define Config_H

// includes all constants necessary, i.e. pin numbers, measurements, etc

// array with all local coordinate frames positions and orientations relative to the global coordinate system of the robot
// (x dist from global coordinate system to local coordinate frame, y dist from global coordinate system to local coordinate frame, angle of rotation)
const float legCoords[6][3] = { {  71.3,  43.0,     PI / 6 },   // leg FR
                                {  71.3, -43.0, 5 * PI / 6 },   // leg FL
                                {     0,  53.0,          0 },   // leg MR
                                {     0, -53.0,         PI },   // leg ML
                                { -71.3,  43.0,    -PI / 6 },   // leg RR
                                { -71.3, -43.0, 7 * PI / 6 } }; // leg RL

// Length of the three links coxa, femur and tibia
const uint8_t coxaLength = 22;
const uint8_t femurLength = 46;
const uint8_t tibiaLength = 88;

// pin numbers for each leg (FL = front left, FR = front right, ML = mid left, RL = rear left)
const uint8_t coxaPinFR = 5;
const uint8_t femurPinFR = 6;
const uint8_t tibiaPinFR = 4;

const uint8_t coxaPinFL = 13;
const uint8_t femurPinFL = 12;
const uint8_t tibiaPinFL = 15;

const uint8_t coxaPinMR = 8;
const uint8_t femurPinMR = 9;
const uint8_t tibiaPinMR = 10;

const uint8_t coxaPinML = 11;
const uint8_t femurPinML = 8;
const uint8_t tibiaPinML = 9;

const uint8_t coxaPinRR = 12;
const uint8_t femurPinRR = 13;
const uint8_t tibiaPinRR = 14;

const uint8_t coxaPinRL = 7;
const uint8_t femurPinRL = 6;
const uint8_t tibiaPinRL = 5;

// offsets in degrees for each motor
const int8_t coxaOffsetFR = 1;
const int8_t femurOffsetFR = 0;
const int8_t tibiaOffsetFR = 4;

const int8_t coxaOffsetFL = 0;
const int8_t femurOffsetFL = -5;
const int8_t tibiaOffsetFL = 6;

const int8_t coxaOffsetMR = -2;
const int8_t femurOffsetMR = -4;
const int8_t tibiaOffsetMR = 8;

const int8_t coxaOffsetML = -10;
const int8_t femurOffsetML = -5;
const int8_t tibiaOffsetML = 4;

const int8_t coxaOffsetRR = -5;
const int8_t femurOffsetRR = -5;
const int8_t tibiaOffsetRR = -4;

const int8_t coxaOffsetRL = -2;
const int8_t femurOffsetRL = 0;
const int8_t tibiaOffsetRL = 5;

// pins of the push-buttons on every leg
const uint8_t buttonFR = 12;
const uint8_t buttonFL = 9;
const uint8_t buttonMR = 14;
const uint8_t buttonML = 10;
const uint8_t buttonRR = 8;
const uint8_t buttonRL = 11;

// home position of every leg. x,y,z - values
const float homePos[3] = { 0.0, 73.0, 80.0 };
//const float homePos[3] = {0.0, 68.0, 88.0}; // use this if you want 90° angles when at home position
//const float homePos[3] = { 0.0, 73.0, 95.0 }; // for a little more ground clearance

// the loop is executed every [periodMs] milliseconds
const uint16_t periodMs = 10;  // recommended for Arduino Nano 33 BLE Sense
//const uint16_t periodMS = 15; // recommended for Arduino Nano 33 IoT

const uint8_t pwm1Addr = 0x40;
const uint8_t pwm2Addr = 0x41;

#endif /* Config_H */

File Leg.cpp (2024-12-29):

// Leg.cpp

#include "Leg.h"
// uncomment the following line to use higher precision.
#define useFloat

void Leg::setAngle(uint8_t servoPin, int offset, int angleVal) {
  /*
   * sets the angle of a certain servo of the leg to the desired value. All angles in degrees.
   * uint8_t servoPin:  the pin (0-15) of the servo on the pwm module
   * int angle:         the angle (0 - 180) to move the servo to
   *
   */

  servoDriver.setPWM(servoPin, 0, angle(angleVal + offset));
}

bool Leg::moveTo(float xValue, float yValue, float zValue) {
  /*
   * moves the leg to the given x y z coordinates (in local coordinate system)
   *
   * xValue:    the x-value (left/right) in mm to move the legpoint to
   * yValue:    the y-value (back/forth) in mm to move the legpoint to
   * zValue:    the z-value (height) in mm to move the legpoint to
   *
   * returns:       true if the leg reached the point, false if the point is unreachable
   */

  // flag rises when leg can't reach the desired position
  bool flag = true;
  //calculate the coxa servo angle using atan2. Mirror the result due to orientation of the servo
  //calculate 2 helper variables L1 and L. Used to calculate the two other angles
  float L1 = sqrt((float)xValue * xValue + yValue * yValue);
  float L = sqrt((float)zValue * zValue + (L1 - coxaLength) * (L1 - coxaLength));

  // abort if the desired point is unreachable. Doesn't check for coxa servo (gamma angle)
  if(!isReachable(L1, zValue)){
    return false;
  }

#if defined(useFloat)
  float gamma = atan2(yValue, xValue) * 180 / PI;
  gamma = mapFloat(gamma, 0.0, 180.0, 180.0, 0.0);

  // angle for femur servo
  float alpha = (acos(zValue / L) + acos((tibiaLength * tibiaLength - femurLength * femurLength - L * L) / (-2 * femurLength * L))) * 180 / PI;

  // angle for tibia servo
  float beta = (acos((L * L - tibiaLength * tibiaLength - femurLength * femurLength) / (-2 * tibiaLength * femurLength))) * 180 / PI;

  // mirrors alpha and beta if the leg is on the right side of the robot
  if (rightSide) {
    alpha = mapFloat(alpha, 0.0, 180.0, 180.0, 0.0);
    beta = mapFloat(beta, 0.0, 180.0, 180.0, 0.0);
  }

  // checks whether the angle is in the allowed interval of [40°, 130°] and then sets the coxa servo to the desired angle
  if ((gamma + offsetCoxa) > 40 && (gamma + offsetCoxa) < 130) {
    servoDriver.setPWM(pinCoxa, 0, angleFloat(gamma + offsetCoxa));
  } else {
    flag = false;
  }

  servoDriver.setPWM(pinFemur, 0, angleFloat(alpha + offsetFemur));
  servoDriver.setPWM(pinTibia, 0, angleFloat(beta + offsetTibia));
#else
  int gamma = SpeedTrig.atan2(yValue, xValue) * 180 / PI;
  gamma = map(gamma, 0, 180, 180, 0);

  // angle for femur servo
  int alpha = (SpeedTrig.acos(zValue / L) + SpeedTrig.acos((tibiaLength * tibiaLength - femurLength * femurLength - L * L) / (-2 * femurLength * L))) * 180 / PI;
  // angle for tibia servo
  int beta = (SpeedTrig.acos((L * L - tibiaLength * tibiaLength - femurLength * femurLength) / (-2 * tibiaLength * femurLength))) * 180 / PI;

  // mirrors alpha and beta if the leg is on the right side of the robot
  if (rightSide) {
    alpha = map(alpha, 0, 180, 180, 0);
    beta = map(beta, 0, 180, 180, 0);
  }

  // checks whether the angle is in the allowed interval of [40°, 130°] and then sets the coxa servo to the desired angle
  if ((gamma + offsetCoxa) > 40 && (gamma + offsetCoxa) < 130) {
    servoDriver.setPWM(pinCoxa, 0, angle(gamma + offsetCoxa));
  } else {
    flag = false;
  }

  servoDriver.setPWM(pinFemur, 0, angle(alpha + offsetFemur));
  servoDriver.setPWM(pinTibia, 0, angle(beta + offsetTibia));
#endif

  // save the current position of the leg
  currPos[0] = xValue;
  currPos[1] = yValue;
  currPos[2] = zValue;

  // returns true if nothing went wrong, returns false if a servo couldn't reach the position
  return flag;
}

[[nodiscard]] float Leg::getXVal() {
  // returns the last x-Value in local coordinates
  return currPos[0];
}

[[nodiscard]] float Leg::getYVal() {
  // returns the last y-Value in local coordinates
  return currPos[1];
}

[[nodiscard]] float Leg::getZVal() {
  // returns the last y-Value in local coordinates
  return currPos[2];
}

[[nodiscard]] int Leg::angle(uint8_t pwmAngle) {
  /*
   * Converts an angle between 0° and 180° to the corresponding number of PWM ticks.
   * The min/max values (105/496) have to be tested 
   * pwmAngle:    the angle in degrees to be converted
   * returns:     the number of PWM ticks corresponding to the angle
   */

  // constrain the input to [0,180]. Avoids faulty outputs
  pwmAngle = constrain(pwmAngle, 0, 180);

  // map the angle in degrees to the PWM tick count
  int pwmValue = map(pwmAngle, 0, 180, 105, 496);

  return pwmValue;
}

[[nodiscard]] int Leg::angleFloat(float pwmAngle) {
  /*
   * Converts an angle between 0° and 180° to the corresponding number of PWM ticks.
   * The min/max values (105/496) have to be tested 
   * pwmAngle:    the angle in degrees to be converted
   * returns:     the number of PWM ticks corresponding to the angle
   */

  // constrain the input to [0,180]. Avoids faulty outputs
  pwmAngle = constrain(pwmAngle, 0.0, 180.0);

  // map the angle in degrees to the PWM tick count
  float result = mapFloat(pwmAngle, 0.0, 180.0, 105.0, 496.0);
  int pwmValue = round(result);

  return pwmValue;
}

float Leg::mapFloat(float x, float in_min, float in_max, float out_min, float out_max) {
  return (x - in_min) * (out_max - out_min) / (in_max - in_min) + out_min;
}

[[nodiscard]] bool Leg::touchesGround() {
  return digitalRead(pinPushButton);
}
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

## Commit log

2024-10-20 fixed bug calling isReachable() and updated images
    [Leg.cpp]
2024-11-10 fix loop time measurement
    [Hexapod.cpp, Hexapod_v4.ino]
2024-12-01 Add wiring diagram
    [wiring_diagram.fzz]
2024-12-01 Fixed minor bug in map() during step
    [Hexapod.cpp]
2024-12-05 Upload CAD Files
    [Base.step, Circuit_Board_Clip.step, Coxa_Main.step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]
2024-12-20 Add CAD assembly and stl files
    [Base.step, Circuit_Board_Clip.step, Coxa_Main.step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]
2024-12-30 Add second step example, Add coordinate frame picture
